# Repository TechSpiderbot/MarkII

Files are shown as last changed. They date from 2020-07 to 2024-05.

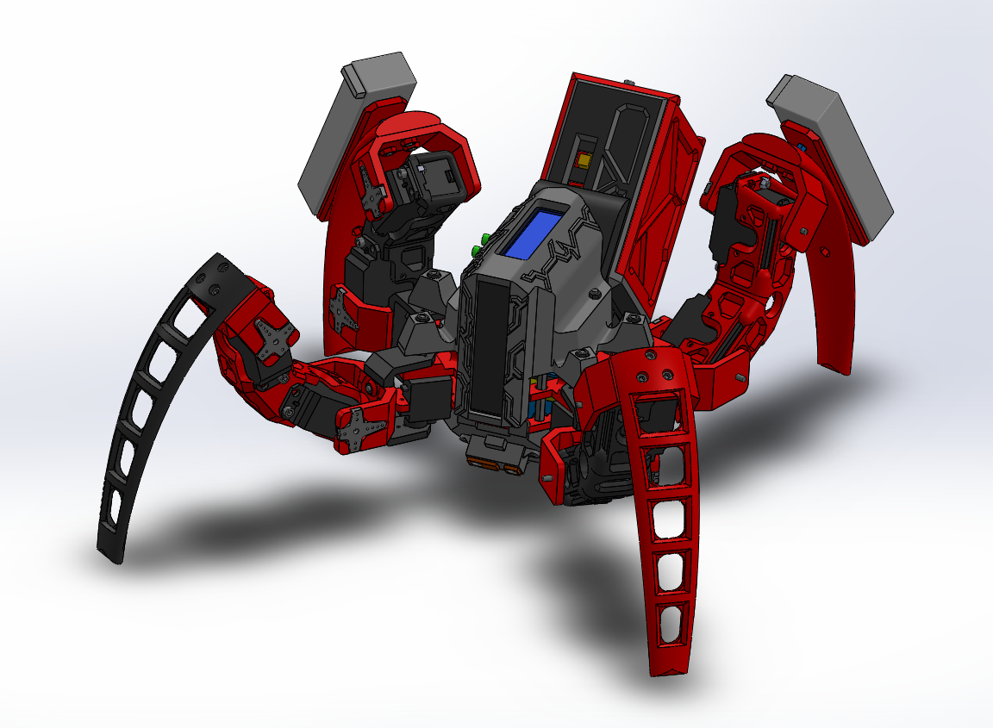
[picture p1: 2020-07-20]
img/mrkII_DES0011.PNG

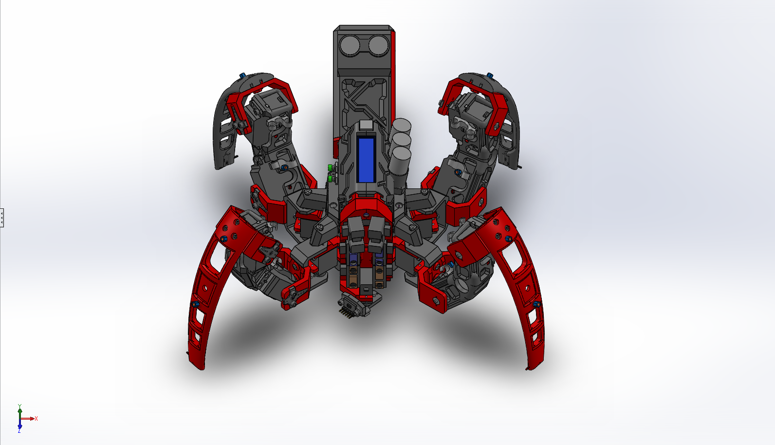
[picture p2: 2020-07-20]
img/mrkII_DES0023.PNG

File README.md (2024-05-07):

# MarkII 

~Scrapped project~

The MrkII TechSpider is an Medium cost, open-source, 3D printed, quadruped robot platform.
The front is designed to be customizable for any type of module. There for the modules can be easily swaped. The cost for the whole robot is around €300. On the backside is a container housing the microcontroller.

The robot is designed for a minimum 3D print build area of 140x140mm
Used material is PLA with a 0.4 nozzle and 30% infill.



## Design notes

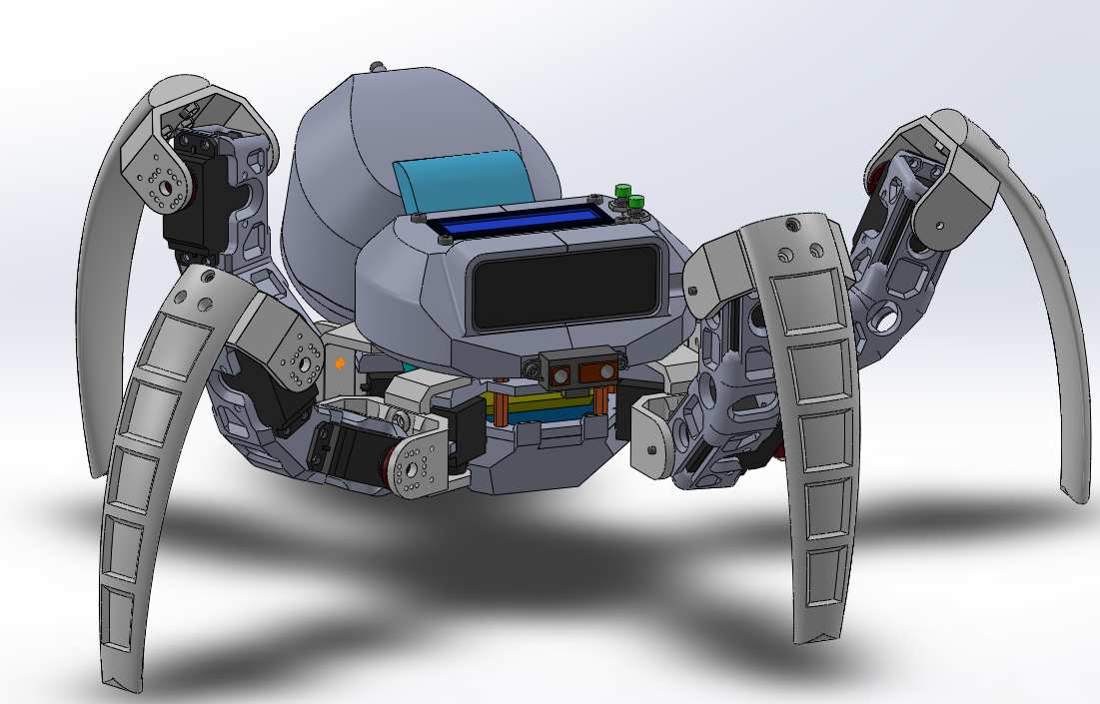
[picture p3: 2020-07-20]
img/mrkII_DES0003.PNG

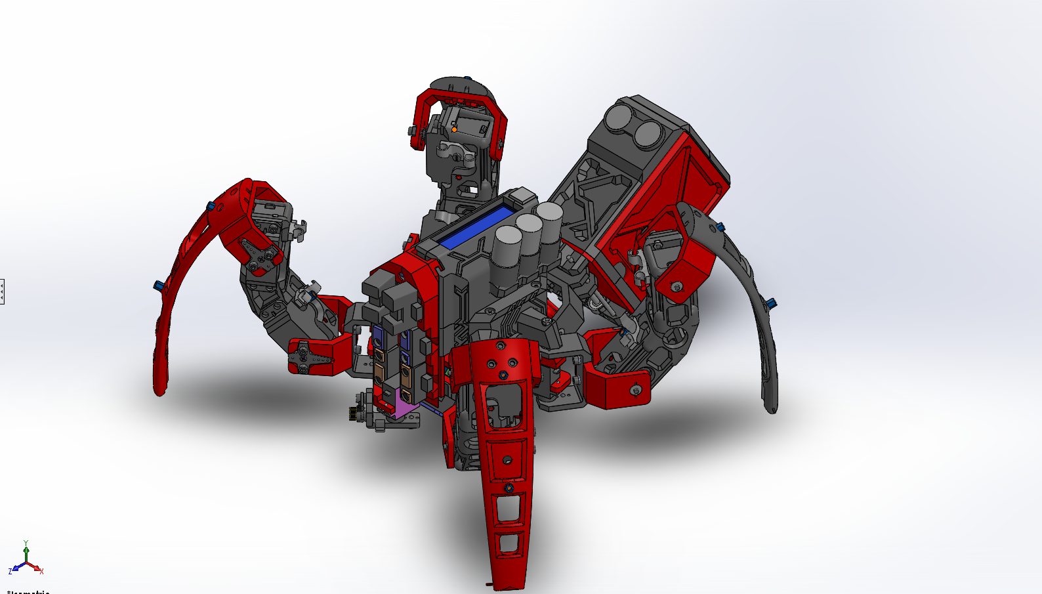
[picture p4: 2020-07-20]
img/mrkII_DES0021.PNG

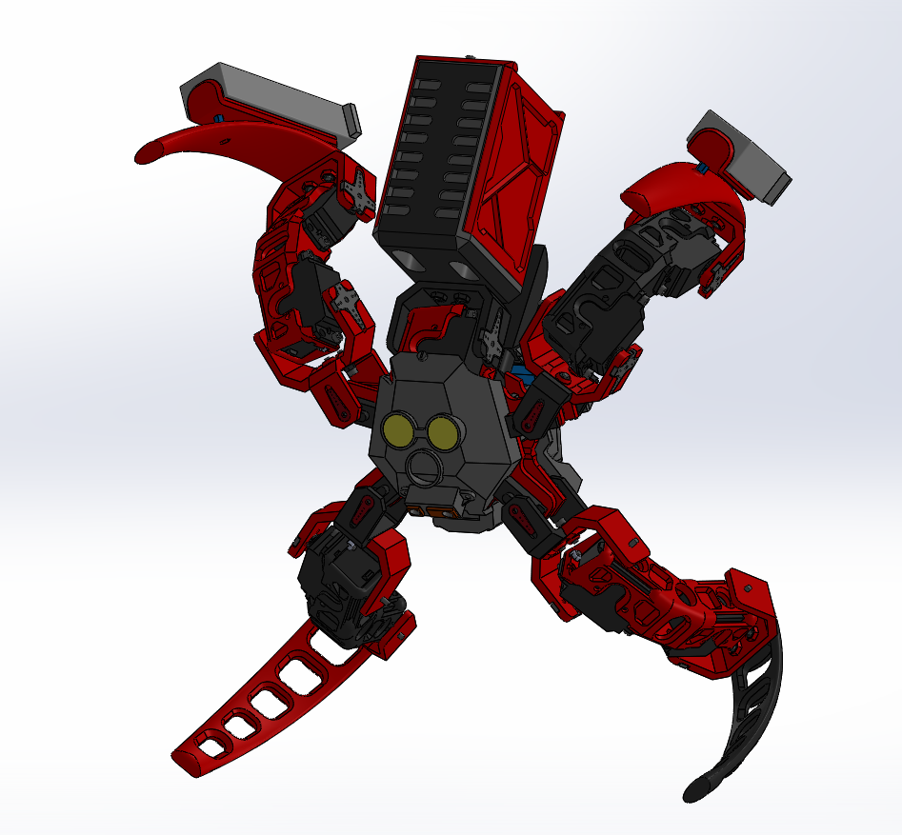
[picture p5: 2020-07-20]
img/mrkII_DES0014.PNG

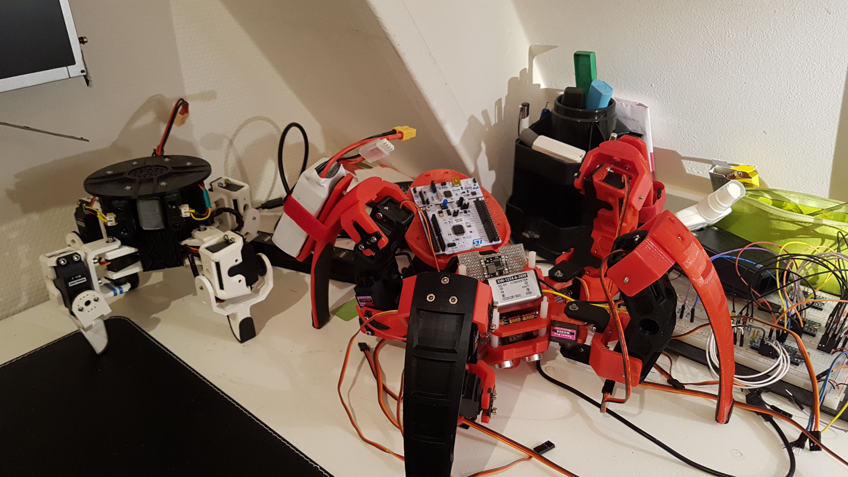
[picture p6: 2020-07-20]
img/mrkII_IMG0003.jpg

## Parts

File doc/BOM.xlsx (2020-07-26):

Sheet: Cover
BOM
Project: | MarkII robot Spider
Versie: | 2.1
Made By: | Geert Huisman
Datum: | 2020-03-12
Printer: | FlashForge Finder
Nozle: | 0.4mm
Type: | PLA
Note: | The front of the robot is customizable! It haves a I2C connection and 3.3V /5V/6V/GND connections for communication and other modules.

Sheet: Hardware
Main Body: |  |  | Type: | count:
 | M2 | round phillips Tapping screw | 5mm | 4
 | M3 | hex inbus | 12mm | 14
 |  | hex inbus | 10mm | 4
 |  | hex inbus | 8mm | 1
 |  | bolt cheese head | 7mm | 4
 |  | round phillips screw | 5mm | 4
 |  | hex flat nut |  | 16
 |  | Nylon Hex Spacers Male to Female | 15+6mm | 18
 |  | Embedded Nuts |  | 11
Parts for single leg
Legs: |  |  | Type: | count:
 | M3 | hex flat nut |  | 9
 |  | hex inbus | 12mm | 5
 |  | hex inbus | 10mm | 2
 |  | hex inbus | 8mm | 2
 |  | round phillips screw | 5mm | 2
 |  | Spring washers |  | 2
 |  | HTSB (spacers) | 5mm | 3
 |  | F693ZZ (bearing) | 3x8x4mm | 3
 |  | Hex Self Tapping scews | 6mm | 5
 |  | bolt | 8mm | 1
 |  | Embedded Nuts |  | 8
 |  | old bike inner tire (used for grip pads on the legs)
Back Body: |  |  | Type: | count:
 | M4 | hex flat nut
 | M3 | hex inbus | 12mm | 12
 |  | hex flat nut |  | 6
 |  | Embedded Nuts |  | 4
 |  | 624ZZ (bearing) | 4x13x5mm | 1
 |  | Nylon Hex Spacers Male to Female | 15+6mm | 2
 |  | socket Hexagon Hex Self Head Tapping scews | 6mm | 2
 |  | F693ZZ (bearing) | 3x8x4mm | 1
 | 3mm | rod from a pc dvd-drive | 82.5mm | 2
 | M1 | bolt | 6mm | 2
 |  | N35 Round Magnet | 10x2 | 1
Front Body: |  |  | Type: | count:
 | M3 | Embedded Nuts |  | 3
 |  | hex inbus | 8mm | 5

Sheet: TOTAL_HARDWARE
 | Type: | Size: | count:
M1 | bolt | 6mm | 2
M2 | round phillips Tapping screw | 5mm | 4
M3 | hex inbus | 12mm | 46
 | hex inbus | 10mm | 12
 | hex inbus | 8mm | 12
 | hex inbus | 6mm | 2
 | Spring washers |  | 8
 | hex flat nut |  | 60
 | Embedded Nuts |  | 50
 | bolt cheese head | 7mm | 8
 | round phillips screw | 5mm | 8
 | socket Hexagon Hex Self Head Tapping scews | 6mm | 22
 | Nylon Hex Spacers Male to Female | 15+6mm | 20
 | HTSB (spacers) | 5mm | 12
M4 | 624ZZ (bearing) | 4x13x5mm | 13
 | hex flat nut |  | 1
Other
3mm | rod from a pc dvd-drive | 82.5mm | 2
 | N35 Round Magnet | 10x2 | 1
 | old bike inner tire (used for grip pads on the legs) |  | 1

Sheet: 3D Printed Parts
Main Body: |  | Count:
 | BODY_arduinoNanoBracket | 1x
 | BODY_capBot | 1x
 | BODY_capTop | 1x
 | BODY_displayClips | 2x
 | BODY_frame1 | 1x
 | BODY_frame2 | 1x
 | BODY_frame3 | 1x
 | BODY_PS2Bracket | 1x
 | BODY_servoBracket1 (embedded nuts) | 1x | (There are 2 versions that can be used "bracket1" or "bracket2" the differents are: one uses embedded nuts while the other uses flat nuts)
 | BODY_servoBracket2
Legs:
 | TIBIA | 4x
 | TIBIA_bracket | 4x
 | TIBIA_batteryHolder | 4x
 | FEMUR | 4x
 | FEMUR_bracket | 4x
 | COXA_bracket | 4x
 | Single_cable_bracket | 8x | (There are 2 versions that can be used "Single" or "Duo" cable brackets)
 | Duo_cable_bracket
Back Body:
 | CONTAINER | 1x
 | CONTAINER_sidePlate | 1x
 | CONTAINER_plate | 1x
 | CONTAINER_railBotBracket | 1x
 | CONTAINER_railTopBracket | 1x
 | CONTAINER_railGlider | 1x
 | CONTAINER_bracket | 1x
Front Body:
 | HEAD_slide | 1x
 | HEAD_module1 | 1x
 | HEAD_moduleArm | 1x

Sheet: Electronic components
Main Body: |  | Count: | Example price
 | HC-SR04 Ultrasone sensor | 1 | €2.50 | €2.50
 | MG996R 55g Gear Servo Motor | 1 | €3.60 | €3.60
 | MPU-6050 | 1 | €1.17 | €1.17
 | GP2Y0A41SK0F | 1 | €5.00 | €5.00
 | PCA9685 16 Channel 12bit PWM Servo motor Driver (https://www.ebay.com/itm/PCA9685-16-Channel-12bit-PWM-Servo-motor-Driver-I2C-Module-Robot-ASS/263464876539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) | 1 | €2.28 | €2.28
 | DC12V To DC6V 6A 36W Aluminum Step Down Power Supply (https://www.ebay.com/itm/DC12V-To-DC6V-6A-36W-Aluminum-Step-Down-Power-Supply-Converter-Regulator-Module/182827563833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) | 1 | €5.00 | €5.00
 | Arduino Nano | 2 | €3.50 | €7.00
 | PS2 Controller kit | 1 | €10.00 | €10.00
 | Custom cable distribution pcb | 1 | €5.00 | €5.00
 | Custom signal pcb | 1 | €5.00 | €5.00
 | Lockless Momentary ON/OFF Push button Switch | 2 | €2.25 | €4.50
 | I2C Interface 16X2 Character LCD Module Display (blue) | 1 | €3.00 | €3.00
 | GY-271 HMC5883L triple Compas | 1 | €4.00 | €4.00
 | WT61 (advanced compass) | 1 | €31.00 | €31.00
 | 25V 10000uF High Frequency Elcos 18x35mm | 3 | €1.70 | €5.10
Parts for single leg
Legs: | Type: | Count:
 | MG996R 55g Gear Servo Motor | 1 | €3.60 | €3.60
 | ~~VS-2 servo motor (hobby servo)~~ | ~~1~~ | €0.00 | €0.00
 | MG90S Micro Metal Gear 9g Servo (screws for mounting is included) | 1 | €3.50 | €3.50
 | 1.27mm Pitch 16 Pin Flat IDC Ribbon (flatcable for extention)
 | Cable sleeve M3
 | High Accuracy 10g-1kg Pressure Sensor Smart Flexible Thin Film Force Sensor | 1 | €4.50 | €4.50
 | Custom sensor pcb | 1 | €5.00 | €5.00
Back Body:
 | M4 GA12 N20 DC (500RPM) 100mm/6V | 1 | €5.00 | €5.00
 | NUCLEO-F411RET6 | 1 | €20.00 | €20.00
 | DRV8833 motor driver | 1 | €1.70 | €1.70
 | Mini Push Button Switch | 1 | €1.19 | €1.19
 | HC-SR04 Ultrasone sensor | 1 | €2.55 | €2.55
 | NRF24L01 2.4Ghz | 2 | €3.80 | €7.60
Front Body: |  | Count:
 | Arduino Nano | 1 | €3.50 | €3.50
 | GP2Y0A41SK0F | 2 | €5.00 | €10.00
 | GP2Y0A21YK0F | 2 | €5.00 | €10.00
 | GP2Y0A02YK0F | 2 | €6.50 | €13.00
 | GY-VL53L0XV2 Time of flight distance sensor (https://www.ebay.com/itm/GY-VL53L0XV2-VL53L0X-Time-of-Flight-Distance-Sensor-Breakout-Module/322328103831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) | 1 | €7.00 | €7.00
 | MG90S Micro Metal Gear 9g Servo (screws for mounting is included) | 1 | €3.60 | €3.60
 | Custom signal pcb | 1 | €5.00 | €5.00
 |  |  | €171.44 | €200.89 | Totall

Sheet: TOTAL_ELECTRONICS
Module: | Count:
raspberry pi + sd card | 1
arduino pro mini | 2
NRF24L01 | 2
Arduino Nano | 3
MG996R 55g Gear Servo Motor | 5
MG90S Micro Metal Gear 9g Servo (screws for mounting is included) | 5
VS-2 servo motor (hobby servo) | 4 | (If unable to find these sevos, it's also possible to use the MG996R instead )
HC-SR04 Ultrasone sensor | 2
MPU-6050 | 1
PS2 Controller kit | 1
Lockless Momentary ON/OFF Push button Switch | 2
I2C Interface 16X2 Character LCD Module Display (blue) | 1
GY-271 HMC5883L triple Compas | 1
25V 10000uF High Frequency Elcos 18x35mm | 3
High Accuracy 10g-1kg Pressure Sensor Smart Flexible Thin Film Force Sensor | 4
PCA9685 16 Channel 12bit PWM Servo motor Driver (https://www.ebay.com/itm/PCA9685-16-Channel-12bit-PWM-Servo-motor-Driver-I2C-Module-Robot-ASS/263464876539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) | 1
DC12V To DC6V 6A 36W Aluminum Step Down Power Supply (https://www.ebay.com/itm/DC12V-To-DC6V-6A-36W-Aluminum-Step-Down-Power-Supply-Converter-Regulator-Module/182827563833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) | 1
M4 GA12 N20 DC (500RPM) 100mm/6V | 1
DRV8833 motor driver | 1
Mini Push Button Switch | 1
GY-VL53L0XV2 Time of flight distance sensor (https://www.ebay.com/itm/GY-VL53L0XV2-VL53L0X-Time-of-Flight-Distance-Sensor-Breakout-Module/322328103831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) | 1
GP2Y0A41SK0F | 3
GP2Y0A21YK0F | 2
GP2Y0A02YK0F | 2
NRF24L01 2.4Ghz | 2 | (wire less comunication for future updates)
NUCLEO-F411RET6 | 1
Custom signal front pcb | 2
Custom sensor pcb | 4
Custom cable distribution pcb | 1
1.27mm Pitch 16 Pin Flat IDC Ribbon (flatcable for extention)
Cable sleeve M3

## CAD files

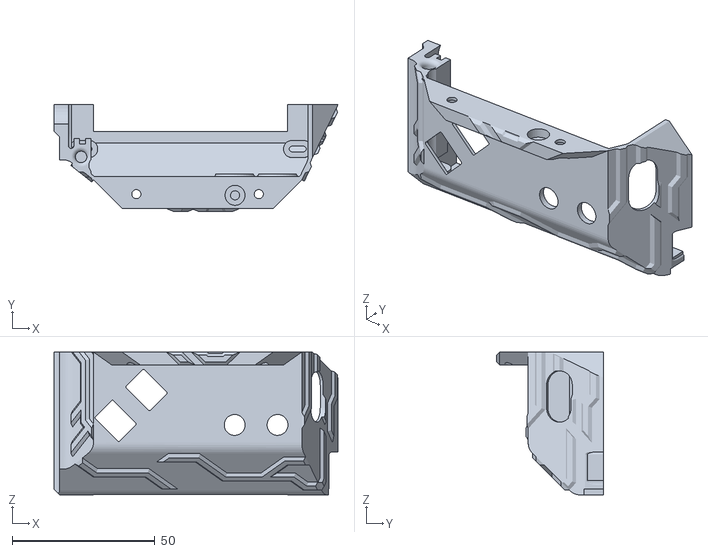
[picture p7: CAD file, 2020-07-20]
cad/0_Main bodyDesign/BODY_capTop/BODY_rightTop.STL
99.4 x 37.3 x 50.0

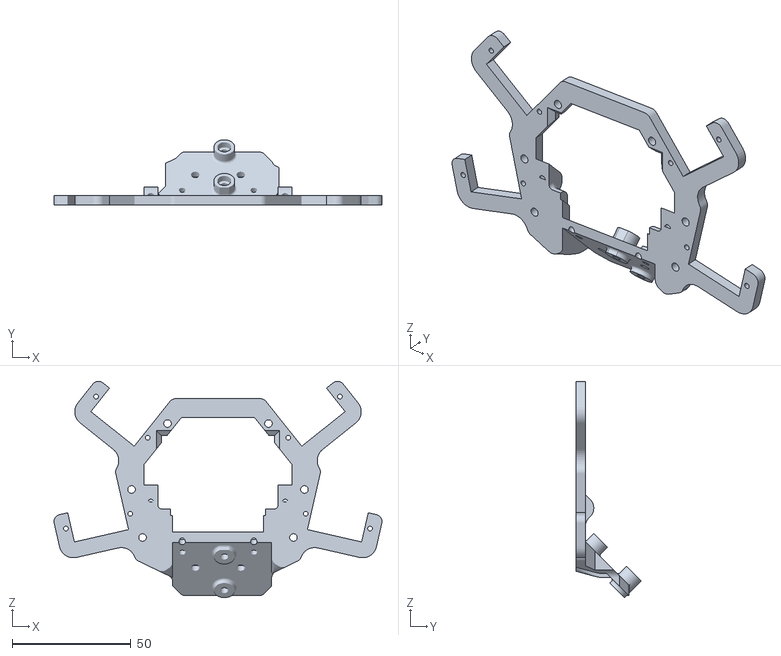
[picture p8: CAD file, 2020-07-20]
cad/0_Main bodyDesign/BODY_frame1.STL
137.9 x 27.5 x 90.9

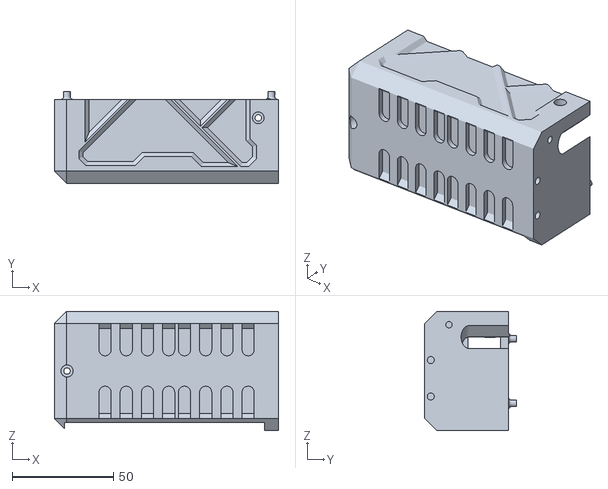
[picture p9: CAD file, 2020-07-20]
cad/1_Back bodyDesign/CONTAINER/CONTAINER_bot.STL
110.8 x 45.3 x 59.0

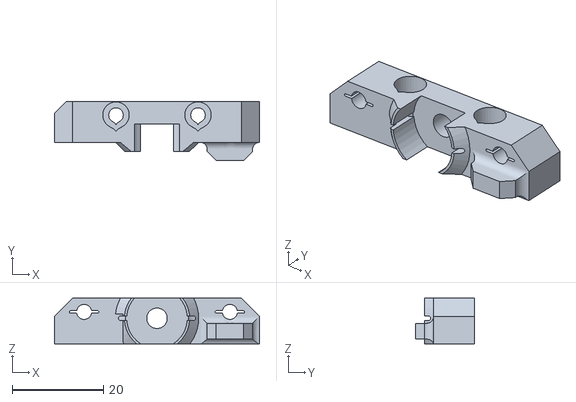
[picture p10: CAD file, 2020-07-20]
cad/1_Back bodyDesign/CONTAINER_railBotBracket.STL
45.0 x 13.0 x 10.00

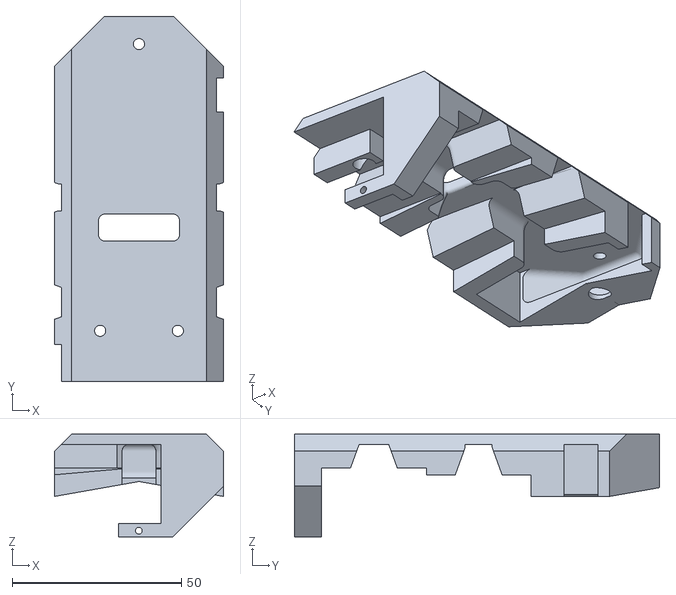
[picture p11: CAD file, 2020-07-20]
cad/2_Front bodyDesign/HEAD_module1.STL
50.0 x 108.0 x 30.4

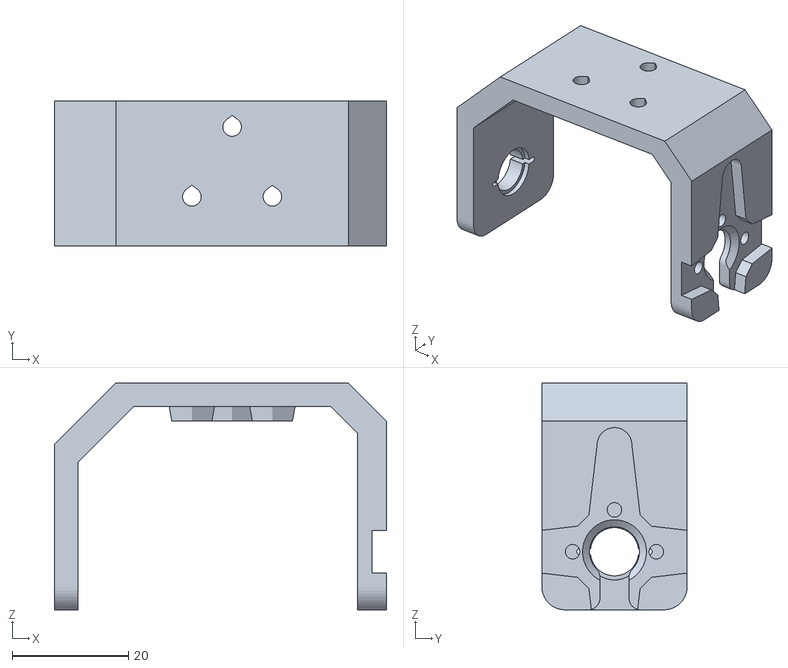
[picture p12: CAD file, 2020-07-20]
cad/3_legDesign/TIBIA_bracket.STL
57.1 x 25.0 x 39.0

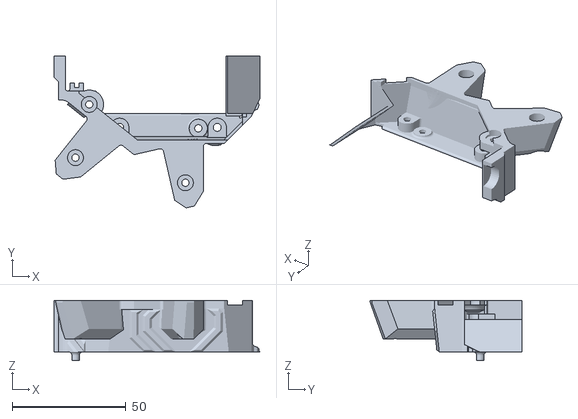
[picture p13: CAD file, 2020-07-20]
cad/0_Main bodyDesign/BODY_capTop/BODY_rightBot.STL
90.5 x 66.7 x 26.4

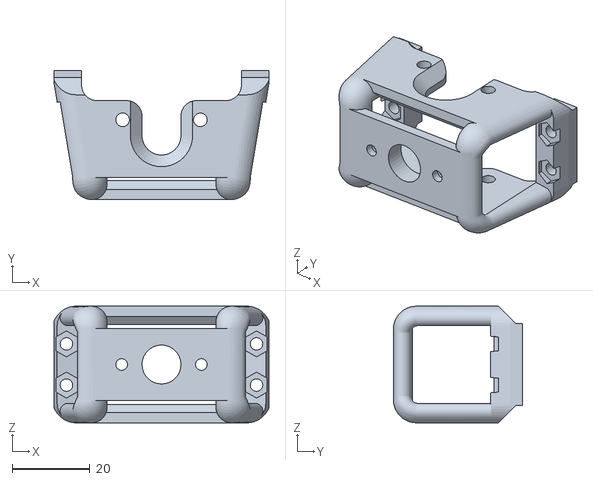
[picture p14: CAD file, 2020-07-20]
cad/0_Main bodyDesign/BODY_servoBracket1.STL
55.3 x 33.3 x 30.0

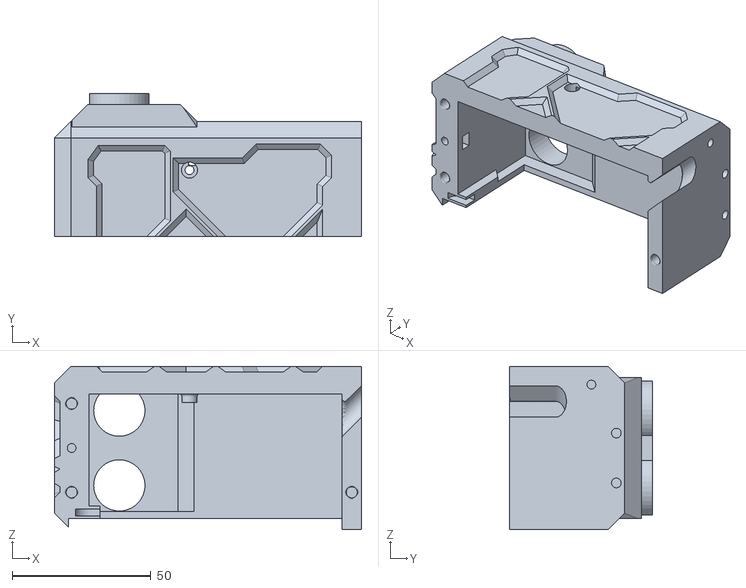
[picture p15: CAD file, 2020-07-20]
cad/1_Back bodyDesign/CONTAINER/CONTAINER_top.STL
110.8 x 51.5 x 59.0

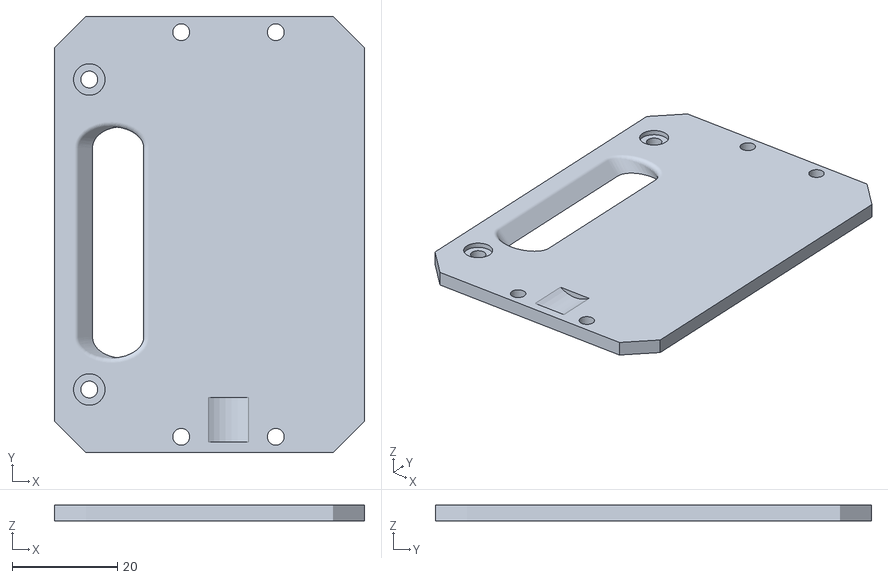
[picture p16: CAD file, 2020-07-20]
cad/1_Back bodyDesign/CONTAINER_plate.STL
59.0 x 83.0 x 3.00

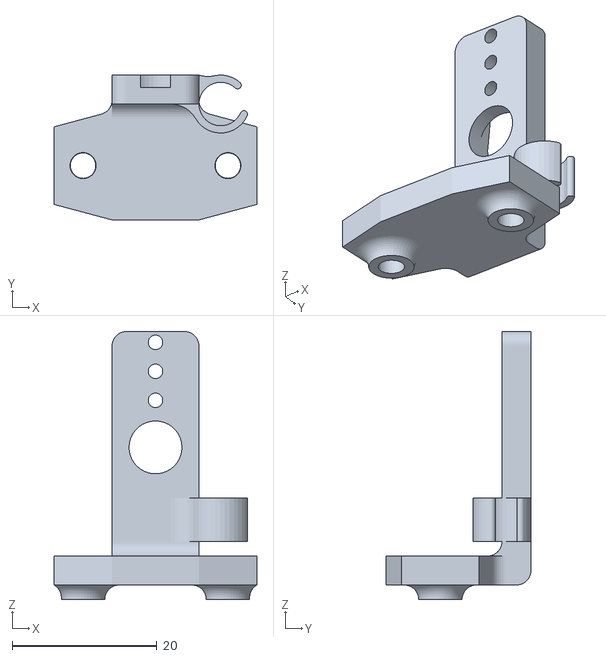
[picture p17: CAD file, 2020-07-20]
cad/2_Front bodyDesign/HEAD_moduleArm.STL
28.0 x 20.0 x 37.0

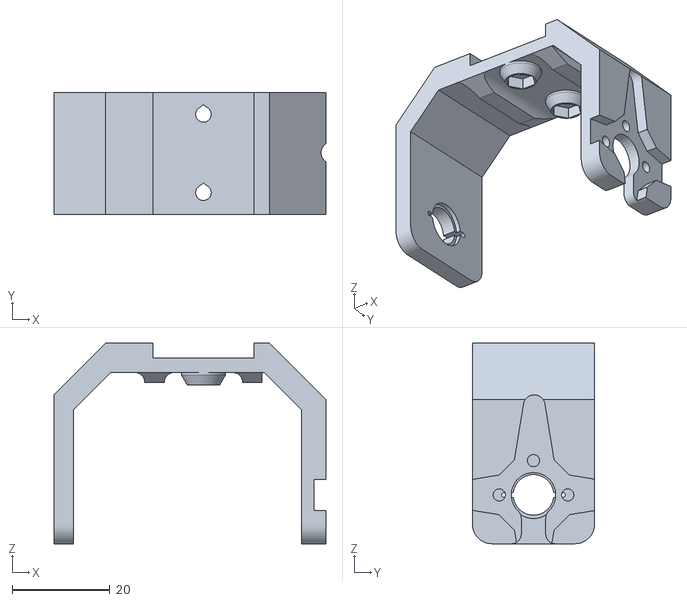
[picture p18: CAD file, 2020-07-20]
cad/3_legDesign/FEMUR_bracket.STL
55.6 x 25.0 x 41.0

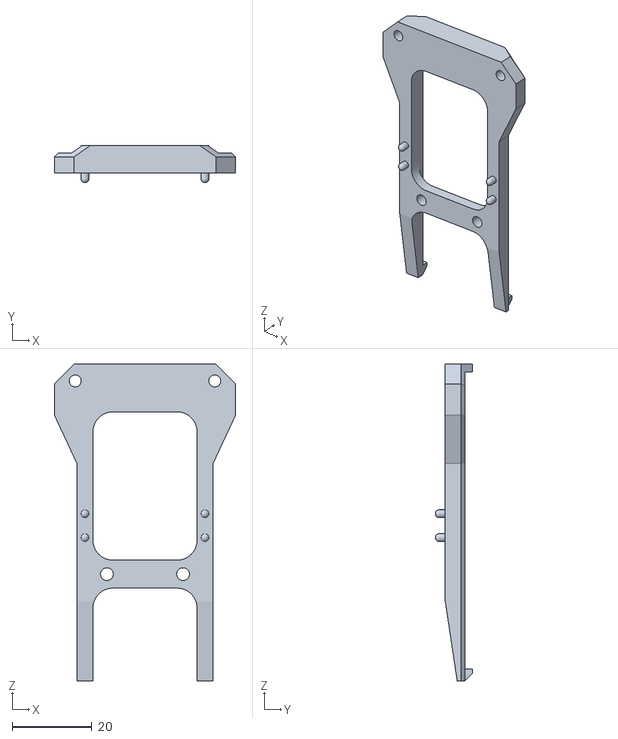
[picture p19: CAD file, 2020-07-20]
cad/0_Main bodyDesign/BODY_PS2Bracket.STL
45.5 x 9.40 x 79.5

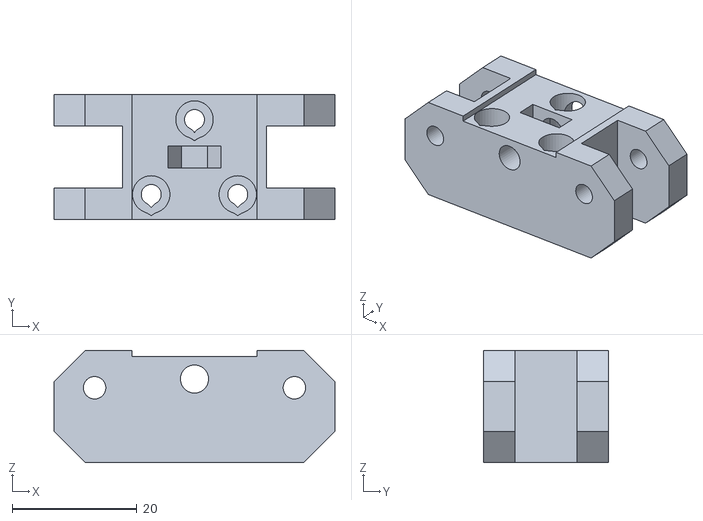
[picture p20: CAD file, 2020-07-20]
cad/1_Back bodyDesign/CONTAINER_railGlider.STL
45.0 x 20.0 x 18.0

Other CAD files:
cad/0_Main bodyDesign/BODY_capTop/BODY_leftBot.STL
cad/2_Front bodyDesign/HEAD_slide.STL
cad/3_legDesign/Single_cable_bracket.STL
cad/0_Main bodyDesign/BODY_capTop/BODY_leftTop.STL
cad/0_Main bodyDesign/BODY_arduinoNanoBracket.STL
cad/0_Main bodyDesign/BODY_capBot.STL
cad/0_Main bodyDesign/BODY_displayClips.STL
cad/0_Main bodyDesign/BODY_frame2.STL
cad/0_Main bodyDesign/BODY_frame3.STL
cad/0_Main bodyDesign/BODY_servoBracket2.STL
cad/1_Back bodyDesign/CONTAINER_bracket.STL
cad/1_Back bodyDesign/CONTAINER_railTopBracket.STL
cad/1_Back bodyDesign/CONTAINER_sidePlate.STL
cad/3_legDesign/COXA_bracket.STL
cad/3_legDesign/Duo_cable_bracket.STL
cad/3_legDesign/FEMUR.STL
cad/3_legDesign/TIBIA.STL
cad/3_legDesign/TIBIA_batteryHolder.STL
cad/5_Shield/shield_cap_2.SLDDRW
cad/5_Shield/shield_plate.SLDDRW

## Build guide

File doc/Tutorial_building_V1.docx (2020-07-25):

Tutorial_Building

Body assembly

Author | Version
Geert Huisman | Setup

Requirements
Hardware M3 | | Amount
| hex flat nut | 9x
12mm | hex inbus | 5x
10mm | hex inbus | 2x
8mm | hex inbus | 2x
5mm | round phillips screw | 4x
| ~~Spring washers~~ | ~~2x~~
5mm | HTSB (spacers) | 3x
3x8x4mm | F693ZZ (bearing) | 2x
6mm | Hex Self Tapping screws | 5x
8mm | bolt | 1x
| Embedded Nuts | 8x
| old bike inner tire (Rubber is used for grip pads on the legs with some glue) | 1x
3D parts | | Amount
| TIBIA | 4x
| TIBIA_bracket | 4x
| TIBIA_batteryHolder | 2x
| FEMUR | 4x
| FEMUR_bracket | 4x
| COXA_bracket | 4x
| Single_cable_bracket (Optional ) | 8x
| Duo_cable_bracket
Electronics | | Amount
| MG996R 55g Gear Servo Motor | 2x
50cm | 1.27mm Pitch 16 Pin Flat IDC Ribbon (flatcable for extention) | 3x
50cm | Cable sleeve M3 | 1x
| High Accuracy 10g-1kg Pressure Sensor Smart Flexible Thin Film Force Sensor | 1x
| Custom pcb (Leg Distr sensor) | 1x
100cm | L125BL25 0.25mm² wire | 6x
15cm | L125BL25 0.25mm² wire | 2x

1. LEGS 4x

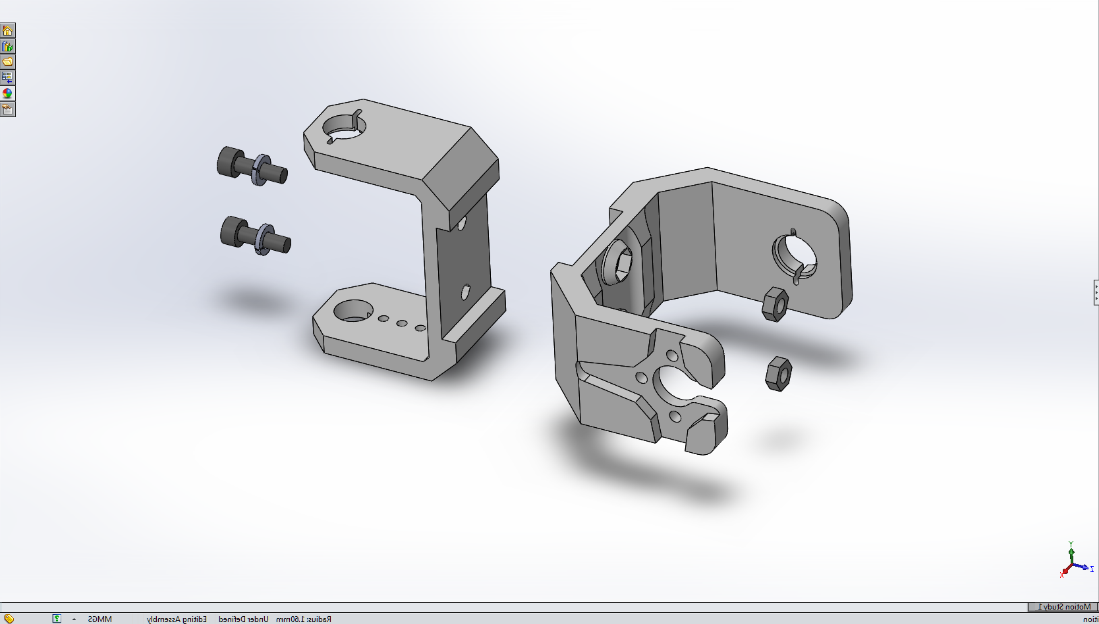
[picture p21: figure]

| 8mm hex inbus hex flat nut ~~Spring washers~~ | 2x 2x ~~2x~~

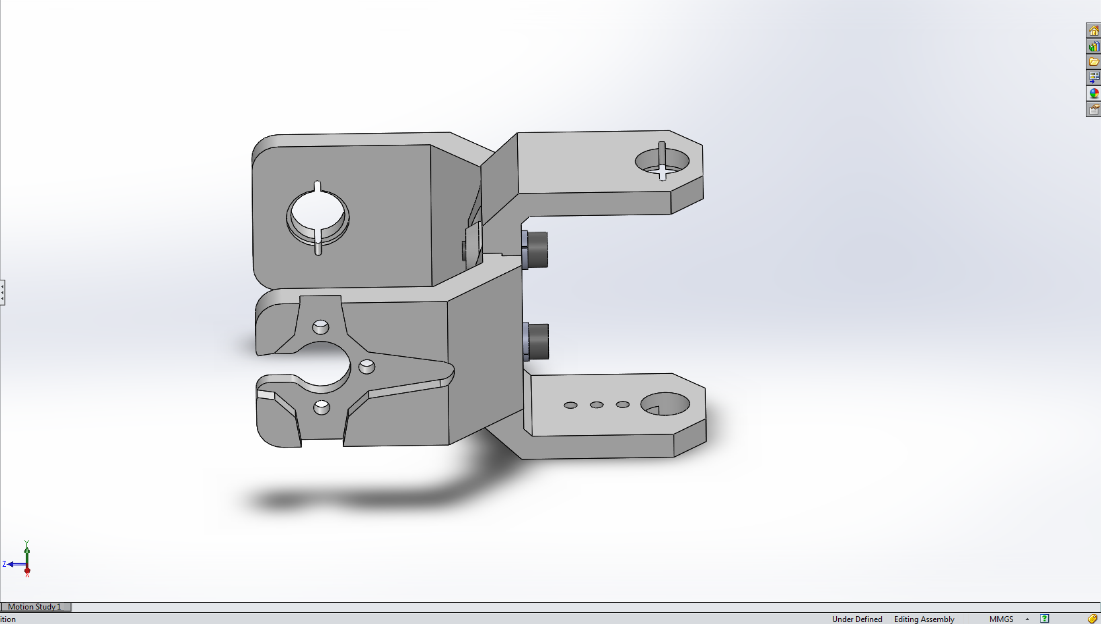
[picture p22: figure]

| Assembly view

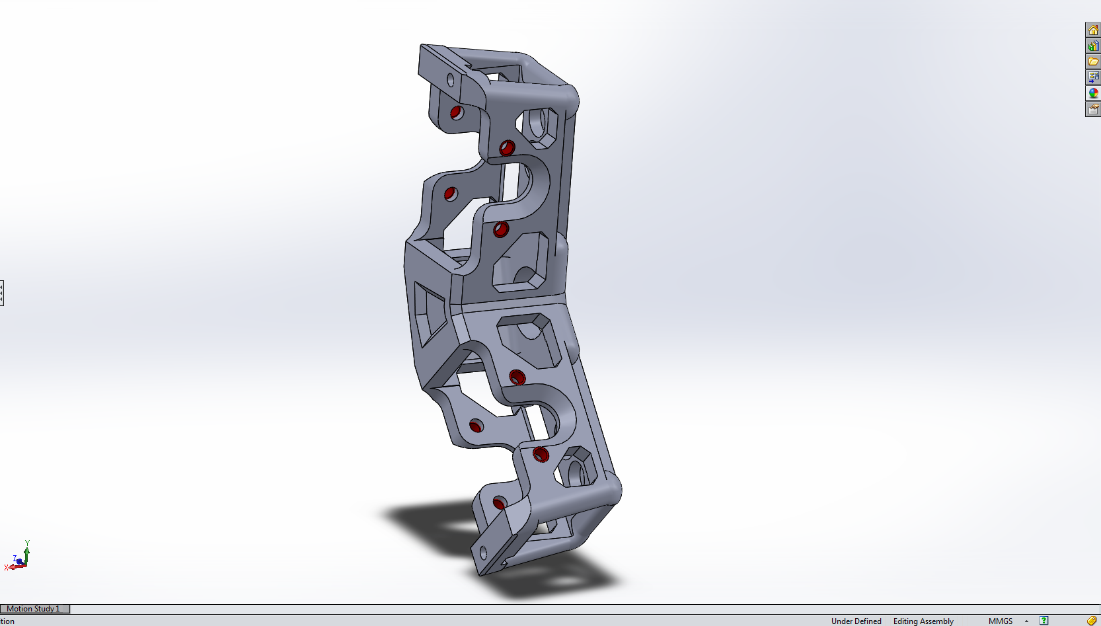
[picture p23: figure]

| Embedded Nuts | 8x

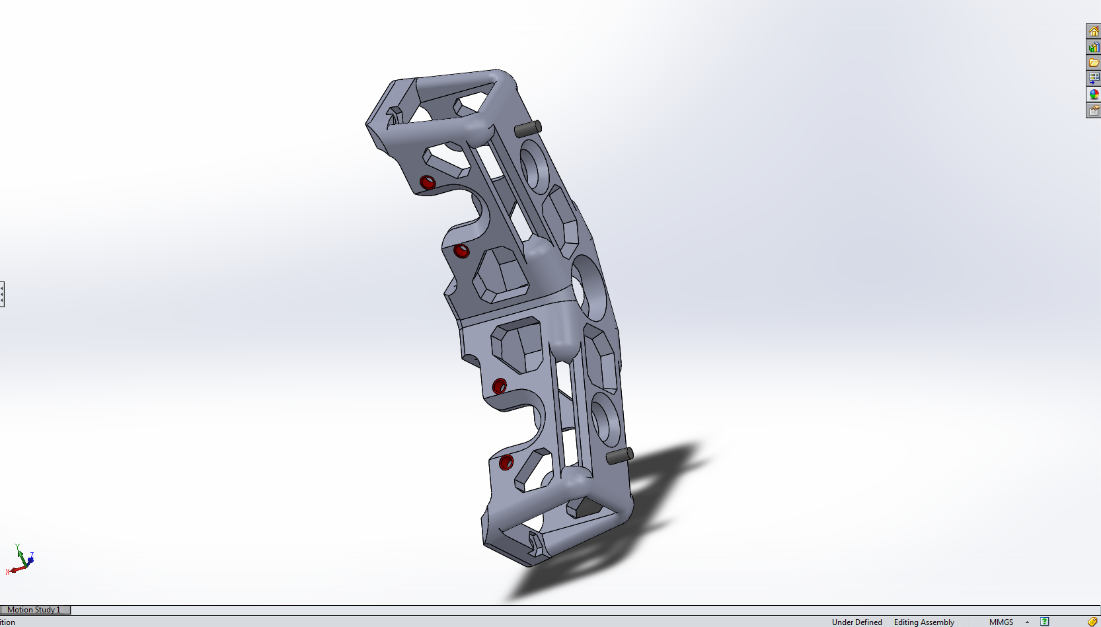
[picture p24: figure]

| 10mm hex inbus | 2x

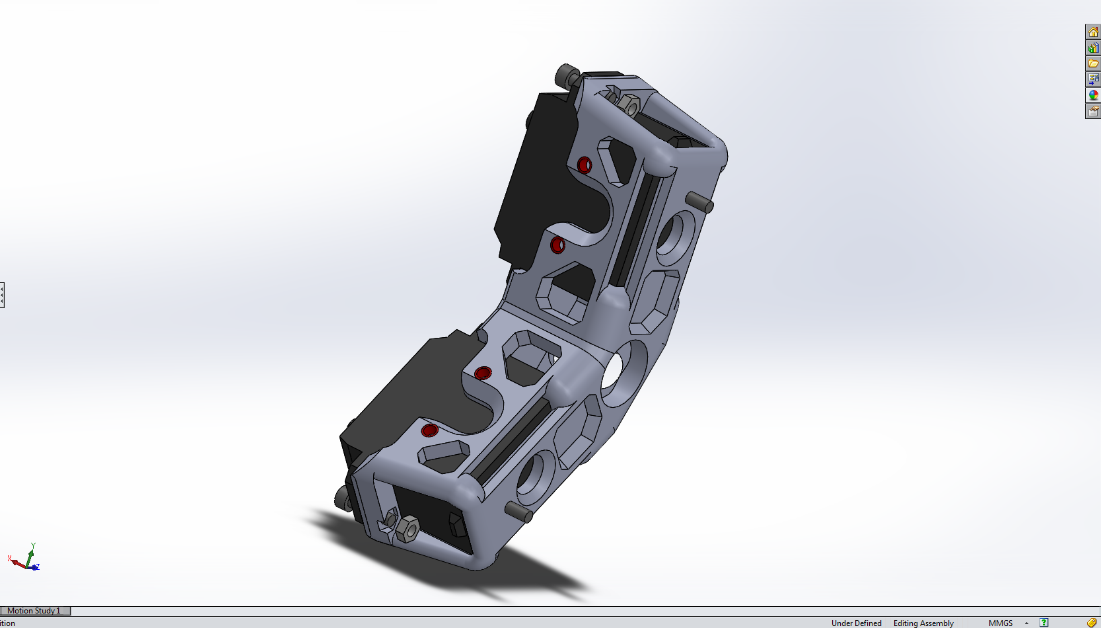
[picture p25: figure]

| MG996R 55g Gear Servo Motor hex flat nut 12mm hex inbus | 2x 2x 2x

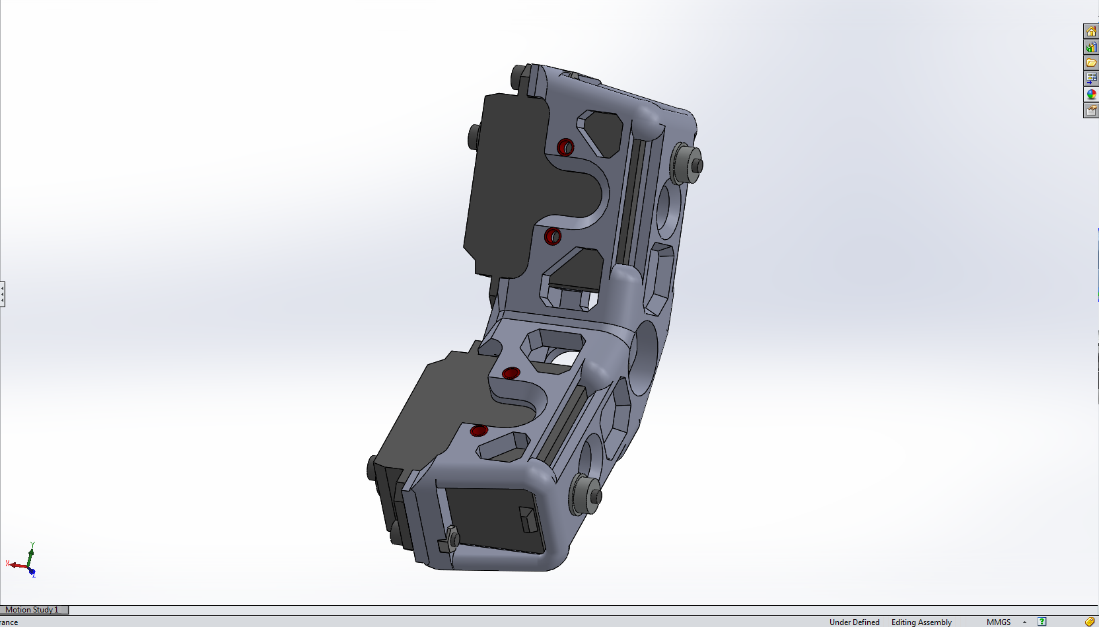
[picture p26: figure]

| 3x8x4mm F693ZZ (bearing) | 2x

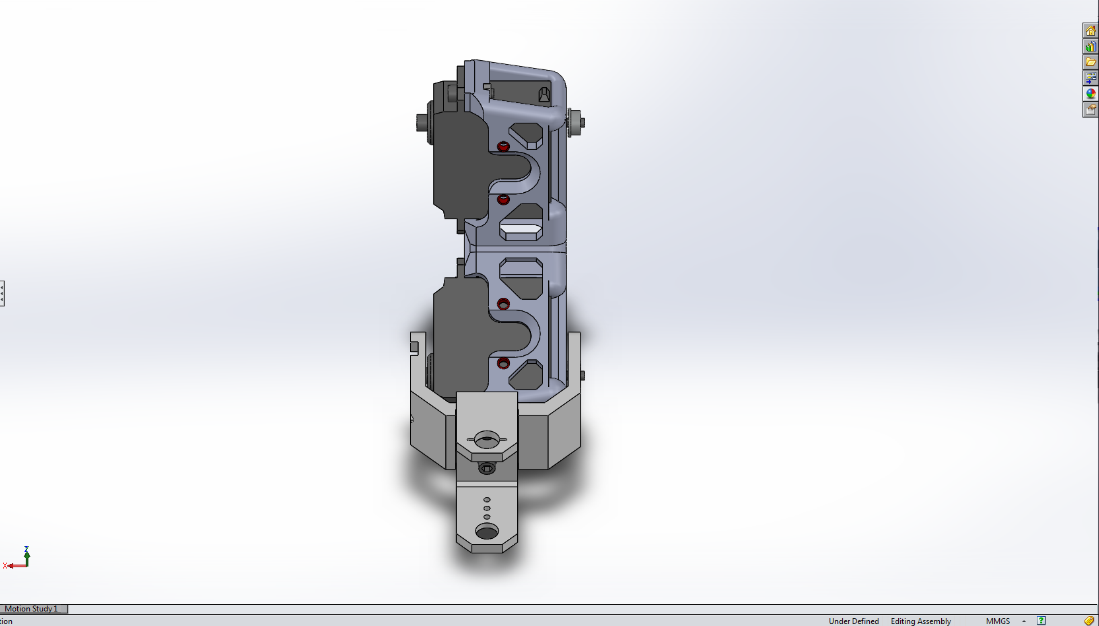
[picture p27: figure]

| Assembly view

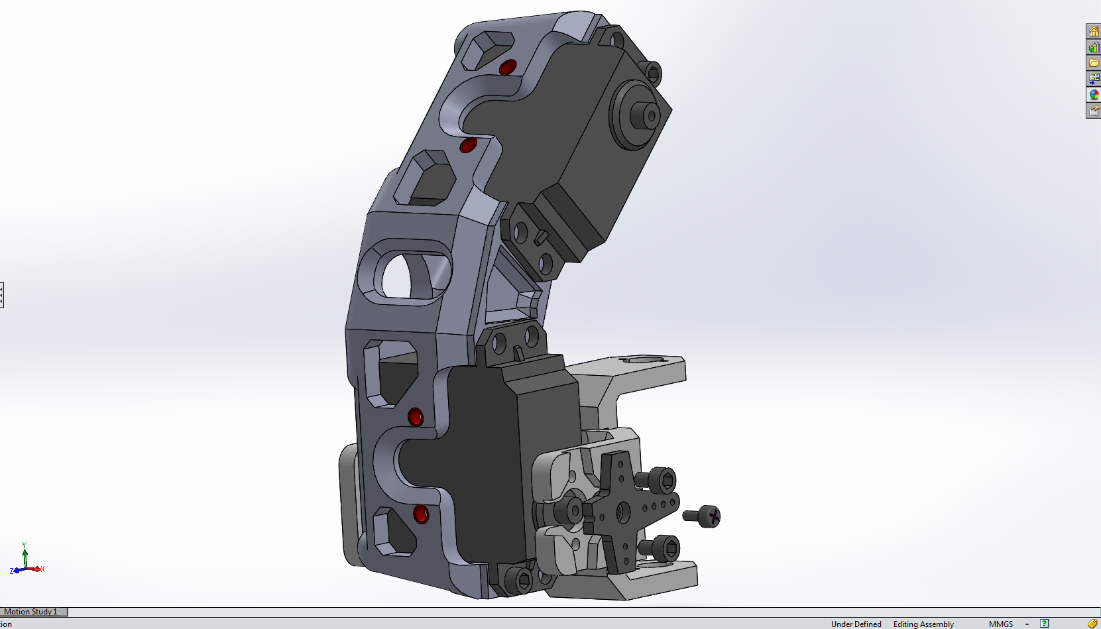
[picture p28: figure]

| (90o in the up position, see picture. Make sure the servo axle is turned 180o) Servo horn 6mm Hex Self Tapping screws | 1x 2x

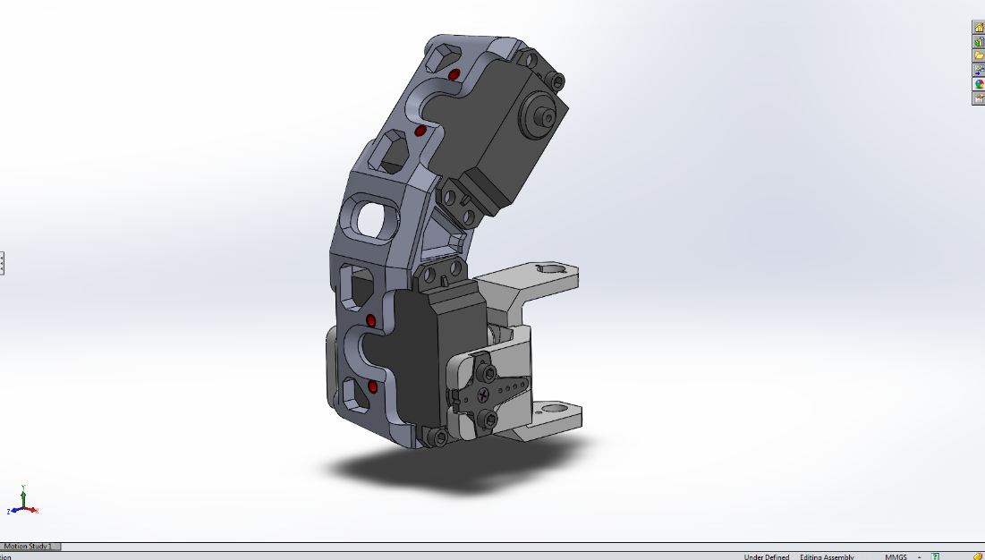
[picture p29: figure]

| Assembly view

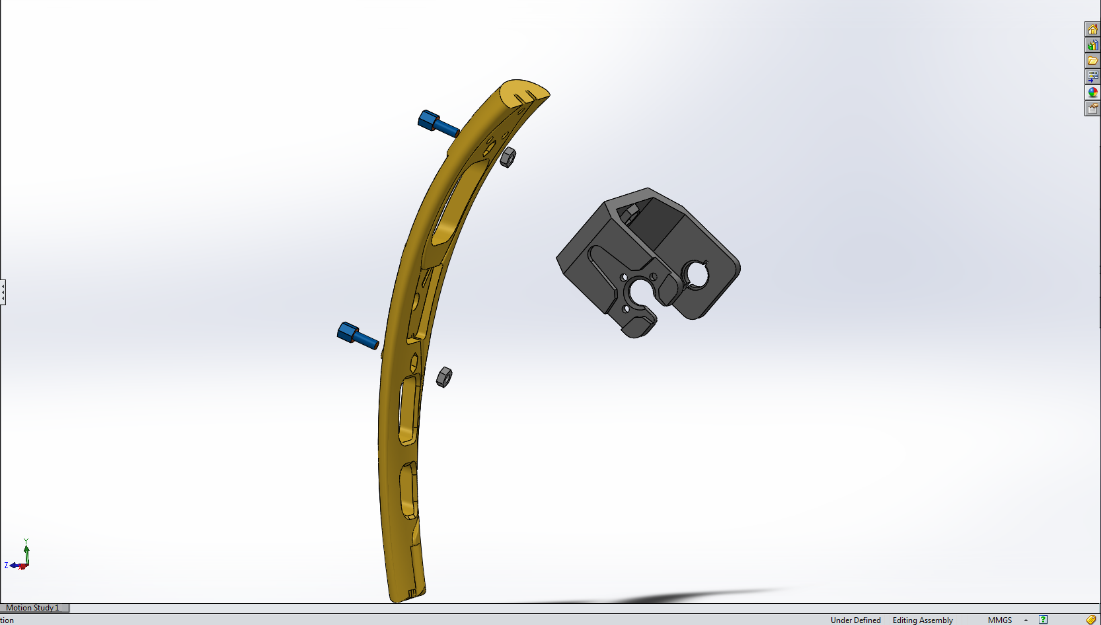
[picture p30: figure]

| hex flat nut 5mm HTSB (spacers) | 2x 2x

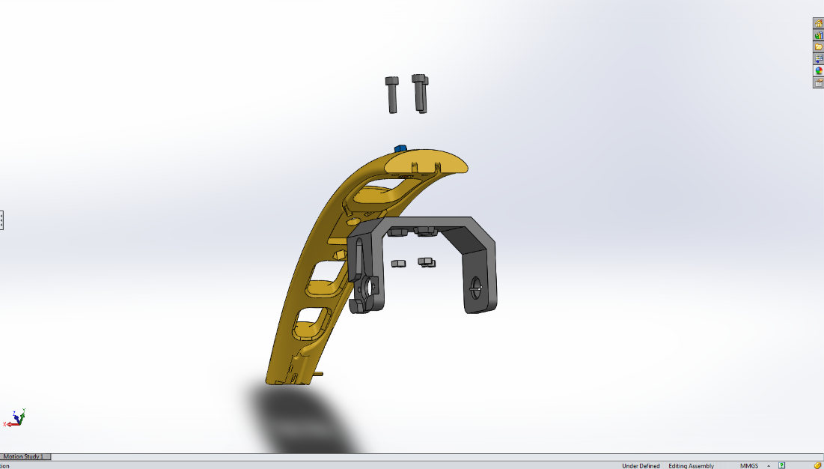
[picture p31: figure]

| hex flat nut 12mm hex inbus | 3x 3x

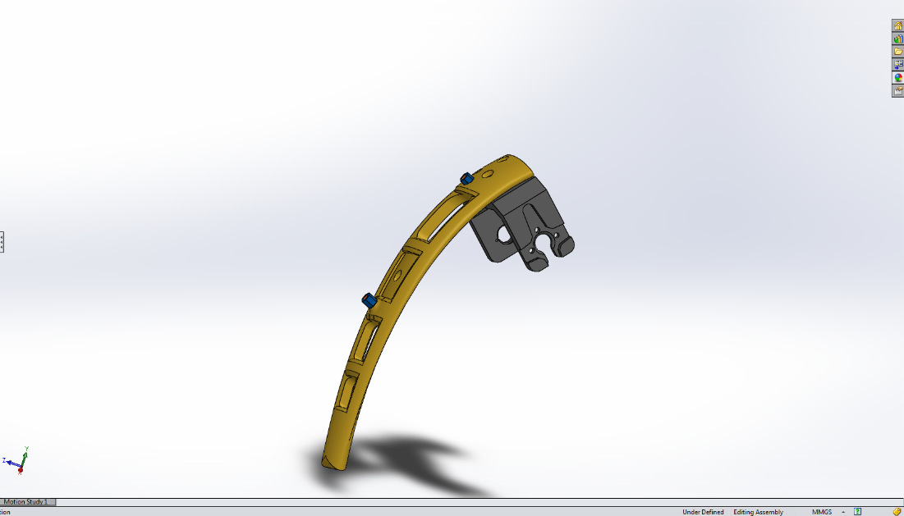
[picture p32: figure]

| Assembly view

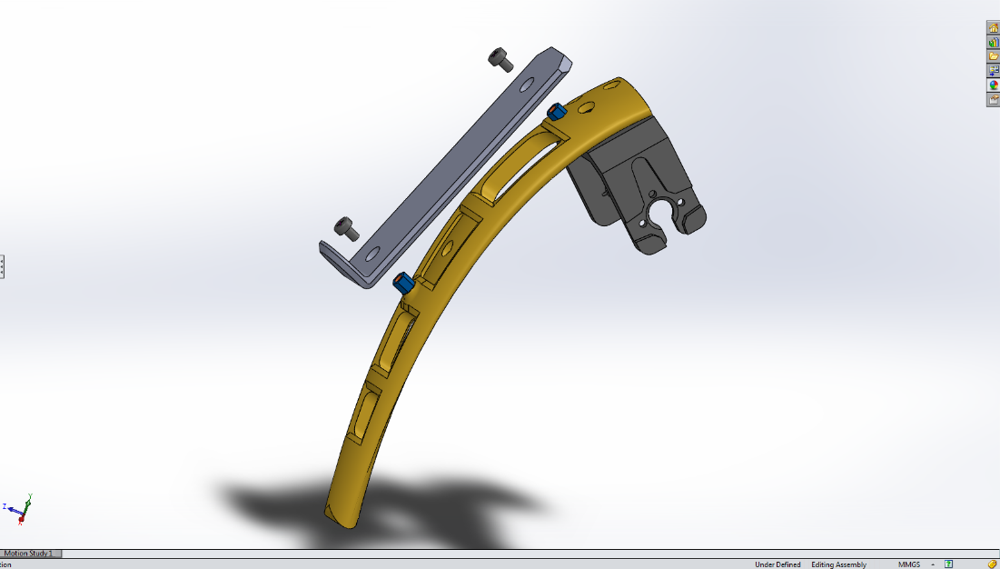
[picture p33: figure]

| round phillips screw | 2x

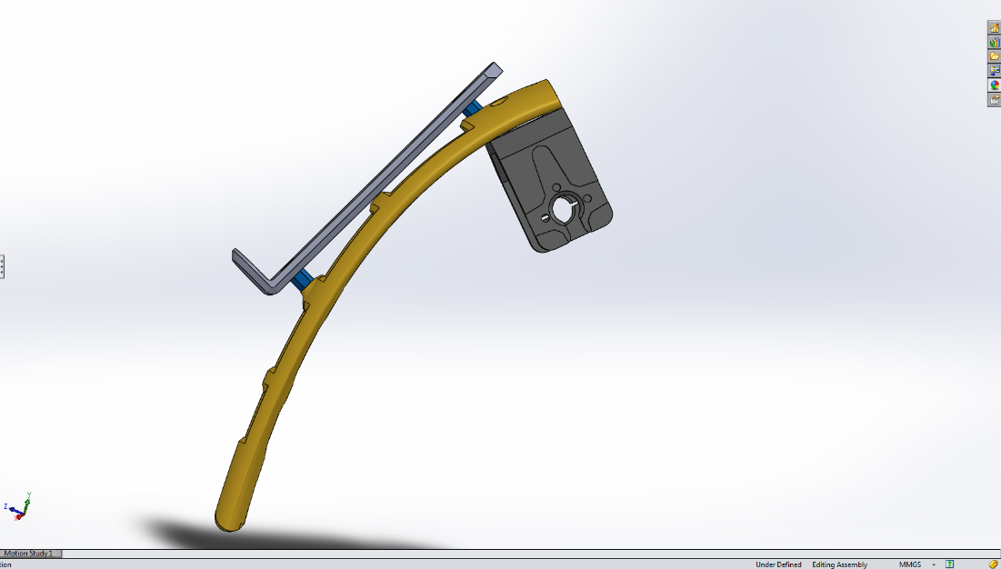
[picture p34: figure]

| Assembly view

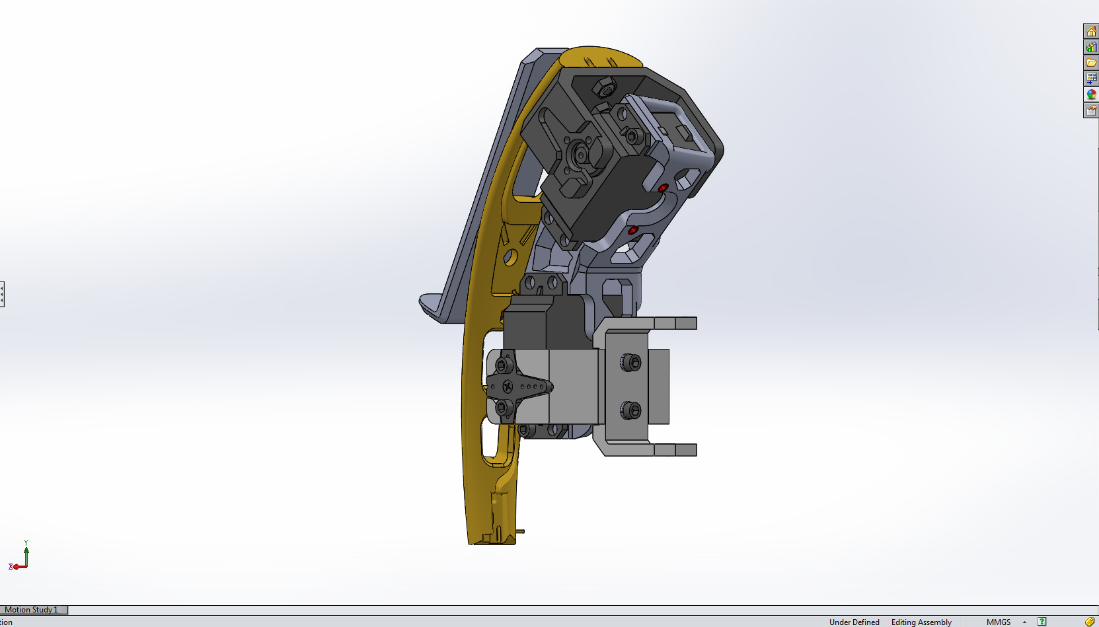
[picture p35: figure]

| Assembly view

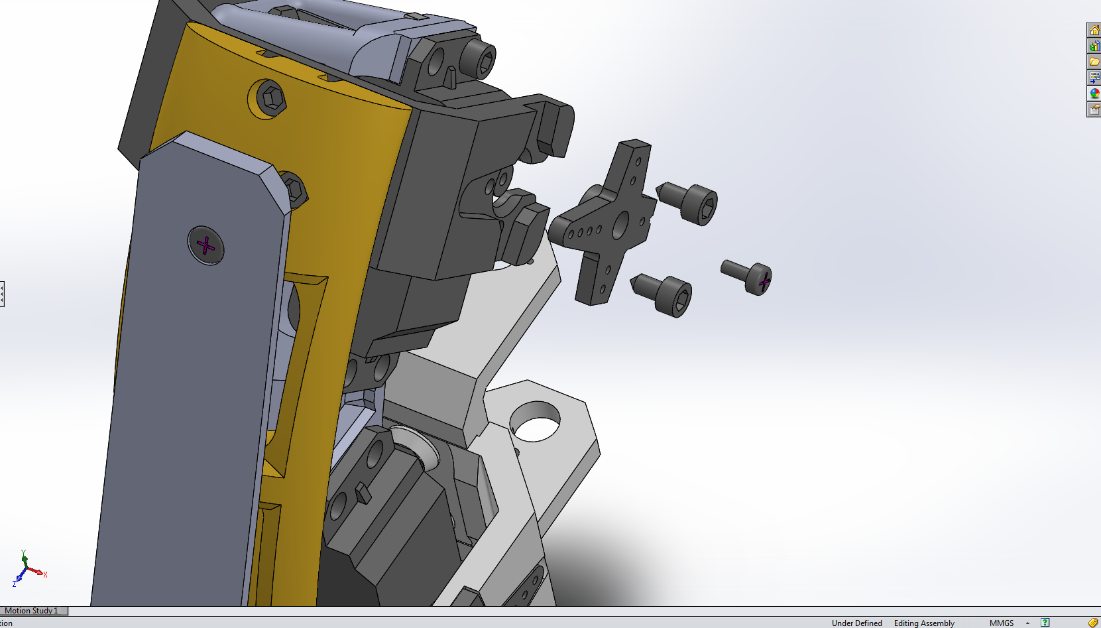
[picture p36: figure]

| (Make sure the servo axle is turned 180o) Servo horn 6mm Hex Self Tapping screws | 1x 2x

MAKII BODY ASSAMBLY 7/25/2020

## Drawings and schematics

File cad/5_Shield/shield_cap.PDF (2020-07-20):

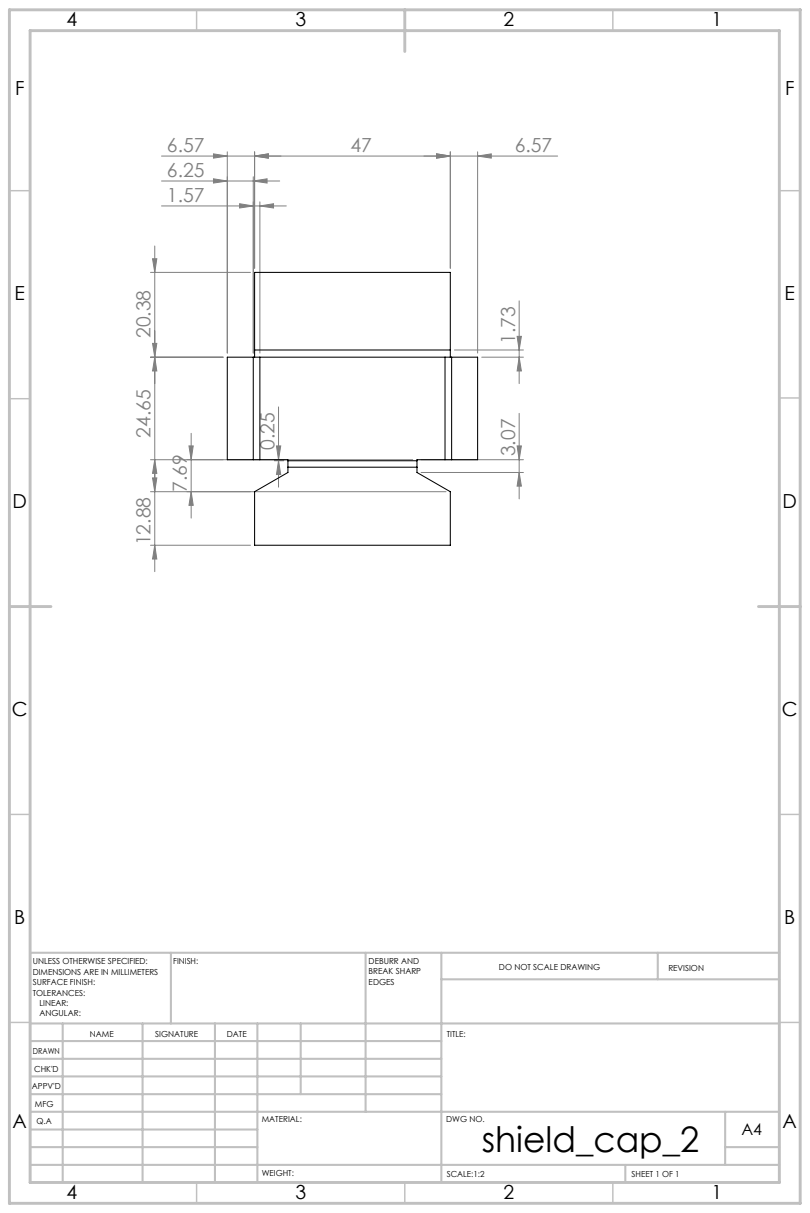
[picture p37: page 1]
FINISH:; DEBURR AND; BREAK SHARP; DO NOT SCALE DRAWING; REVISION; SCALE:1:2; SHEET 1 OF 1

UNLESS OTHERWISE SPECIFIED:
DIMENSIONS ARE IN MILLIMETERS
SURFACE FINISH:
TOLERANCES:
LINEAR:
ANGULAR:

NAME | SIGNATURE | DATE | | | | TITLE:

DRAWN
CHK'D
APPV'D
MFG
Q.A | | | | MATERIAL: | DWG NO. shield_cap_2 | A4

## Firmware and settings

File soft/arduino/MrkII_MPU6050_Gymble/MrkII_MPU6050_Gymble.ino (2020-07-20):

/*
* MASTER Arduino
* Serial communication between container 
* 
* I2C comunication to slaves
* 
*/
#include <RGBLed.h>
/* https://github.com/wilmouths/RGBLed
*/
#include "stdio.h"
#include "I2Cdev.h"
#include "MPU6050_6Axis_MotionApps20.h"

// Arduino Wire library is required if I2Cdev I2CDEV_ARDUINO_WIRE implementation
// is used in I2Cdev.h
#if I2CDEV_IMPLEMENTATION == I2CDEV_ARDUINO_WIRE
#include "Wire.h"
#endif
// ================================================================
// ===               #DEFINE                                    ===
// ================================================================
/* Control keys for reading data
 * ack = enable to read data
 * dis = disable to read data
 *  
 *  the adruino nano will continiue run even when disabled, only the data request is disabled.
 */
#define enableGyroData "ack\n"    // receive confirm 10
#define disableGyroData "dis\n"   // receive confirm 0

#define MAX_OUT_CHARS 16

/* request Gyro data
 *  Yaw   data send i
 *  Pitch data send j
 *  Roll  data send k
 */
#define accesYaw "i\n"
#define accesPitch "j\n"
#define accesRoll "k\n"

#define INTERRUPT_PIN 2  // use pin 2 on Arduino Uno & most boards

// ================================================================
// == Master settings
// ================================================================
/* request head distance data:
 *  demo mode acces with h
 *  
 * request leg sensor data: 
 *  all data update       l
 *  pick serial separated p
 */

#define accesHeadSensor "h\n"
#define accesLegSensor  "l\n"
#define accesLegSeperated "p\n"
/*
 * Define Slave I2C Address
 */
#define HEAD_ADDR 0x06
#define MASTER_ADDR 0x07
#define COMPASS_ADDR 0x08
#define DISTANCE_VALVE 3

// Define counter to count bytes in response
int bcount;
// Define array for return data
int SensorDistance[DISTANCE_VALVE];
int SensorLEGS[8];
int iSensorLEGS;

/*
 * RGB led settings
 */
bool I2C_error = false;
 
#define DATA_SIZE 2
int nucleoData[DATA_SIZE];
int LEG1_DATA[DATA_SIZE];
int LEG2_DATA[DATA_SIZE];
// RGB LED CONFIG
//            RED, GREEN, BLUE
int LEG1_RGB[3] = {11,10,9};
int LEG2_RGB[3] = {6,5,3};

RGBLed led1(LEG1_RGB[0], LEG1_RGB[1], LEG1_RGB[2],COMMON_CATHODE);
RGBLed led2(LEG2_RGB[0], LEG2_RGB[1], LEG2_RGB[2],COMMON_CATHODE);
 
// ================================================================
// == End master settings
// ================================================================


// ================================================================
// == MPU settings
// ================================================================
// class default I2C address is 0x68
// specific I2C addresses may be passed as a parameter here
// AD0 low = 0x68 (default for SparkFun breakout and InvenSense evaluation board)
// AD0 high = 0x69
MPU6050 mpu;
//MPU6050 mpu(0x69); // <-- use for AD0 high

float correct;
int j = 0;

int num = 0;
char  buffer[MAX_OUT_CHARS + 1];

// serial event variable
String inputString = "";      // a String to hold incoming data
bool stringComplete = false;  // whether the string is complete
bool getData = false;

int outp0Value = 0;
int outp1Value = 0;
int outp2Value = 0;

// MPU control/status vars
bool dmpReady = false;  // set true if DMP init was successful
uint8_t mpuIntStatus;   // holds actual interrupt status byte from MPU
uint8_t devStatus;      // return status after each device operation (0 = success, !0 = error)
uint16_t packetSize;    // expected DMP packet size (default is 42 bytes)
uint16_t fifoCount;     // count of all bytes currently in FIFO
uint8_t fifoBuffer[64]; // FIFO storage buffer

// orientation/motion vars
Quaternion q;           // [w, x, y, z]         quaternion container
VectorInt16 aa;         // [x, y, z]            accel sensor measurements
VectorInt16 aaReal;     // [x, y, z]            gravity-free accel sensor measurements
VectorInt16 aaWorld;    // [x, y, z]            world-frame accel sensor measurements
VectorFloat gravity;    // [x, y, z]            gravity vector
float euler[3];         // [psi, theta, phi]    Euler angle container
float ypr[3];           // [yaw, pitch, roll]   yaw/pitch/roll container and gravity vector
float outpValue[3];
// ================================================================
// packet structure for InvenSense teapot demo
// uint8_t teapotPacket[14] = { '$', 0x02, 0, 0, 0, 0, 0, 0, 0, 0, 0x00, 0x00, '\r', '\n' };
// ================================================================


// ================================================================
// ===               INTERRUPT DETECTION ROUTINE                ===
// ================================================================

volatile bool mpuInterrupt = false;     // indicates whether MPU interrupt pin has gone high
void dmpDataReady() {
  mpuInterrupt = true;
}

// ================================================================
// ===                      INITIAL SETUP                       ===
// ================================================================
// reset arduino when does't get an ack
void(* resetFunc) (void) = 0;

void setup() {
  
  // Setup Serial and basic I2C
  // ================================================================
  // join I2C bus (I2Cdev library doesn't do this automatically)
#if I2CDEV_IMPLEMENTATION == I2CDEV_ARDUINO_WIRE
  Wire.begin();
  Wire.setClock(400000); // 400kHz I2C clock. Comment this line if having compilation difficulties
#elif I2CDEV_IMPLEMENTATION == I2CDEV_BUILTIN_FASTWIRE
  Fastwire::setup(400, true);
#endif

  // initialize serial communication
  Serial.begin(115200);
  // reserve 200 bytes for the inputString:
  inputString.reserve(200);
  
  // Setup Gyroscoop
  // ================================================================
  //Serial.println(F("Initializing I2C devices..."));
  mpu.initialize();
  pinMode(INTERRUPT_PIN, INPUT);
  devStatus = mpu.dmpInitialize();
  // supply your own gyro offsets here, scaled for min sensitivity
  mpu.setXGyroOffset(17);
  mpu.setYGyroOffset(-69);
  mpu.setZGyroOffset(27);
  mpu.setZAccelOffset(1551); // 1688 factory default for my test chip

  // make sure it worked (returns 0 if so)
  if (devStatus == 0) {
    // turn on the DMP, now that it's ready
    // Serial.println(F("Enabling DMP..."));
    mpu.setDMPEnabled(true);

    attachInterrupt(digitalPinToInterrupt(INTERRUPT_PIN), dmpDataReady, RISING);
    mpuIntStatus = mpu.getIntStatus();

    // set our DMP Ready flag so the main loop() function knows it's okay to use it
    //Serial.println(F("DMP ready! Waiting for first interrupt..."));
    dmpReady = true;

    // get expected DMP packet size for later comparison
    packetSize = mpu.dmpGetFIFOPacketSize();
  } else {
    // ERROR!
    // 1 = initial memory load failed
    // 2 = DMP configuration updates failed
    // (if it's going to break, usually the code will be 1)
    // Serial.print(F("DMP Initialization failed (code "));
    //Serial.print(devStatus);
    //Serial.println(F(")"));
  }
  Wire.begin(MASTER_ADDR);
  Wire.onReceive(receiveEvent);
}
// ================================================================
// ===                    MAIN PROGRAM LOOP                     ===
// ================================================================
void SetColour();
void CHECK_FLAGS();

void readGyroData();
int readI2C(int);
void readHeadSensorDatarrwd();
void readLegSensorData();

void loop() {
   
  readGyroData();    //READ GYRO DATA 
  
  // send only data on request
  /*
   * IF adruino get an ack\n then 
   * Be active to comunicate by serial
   */
  if (stringComplete){
    //Serial.print(inputString);
    if(inputString == enableGyroData){ //ENABLE: send "ack\n" 
      num = 10;
      sprintf(buffer,"%d",num);
      Serial.println(buffer);
      getData = true;   
    }
    else if(inputString == disableGyroData){ //DISABLE: send "dis\n"
      num = 0;
      sprintf(buffer,"%d",num);
      Serial.println(buffer);
      getData = false; 
    }

    if(getData){
      // == Gyro data ==
      if(inputString == accesYaw){ // I: Send YAW
        //Serial.print("Yaw: ");   
        sprintf(buffer,"%d",outp0Value);
        Serial.println(buffer);
      }
      else if(inputString == accesPitch){ // J: Send Pitch
        //Serial.print("Pitch: "); 
        sprintf(buffer,"%d",outp1Value);
        Serial.println(buffer);
      }
      else if(inputString == accesRoll){ // K: Send Roll
        //Serial.print("Roll: ");  
        sprintf(buffer,"%d",outp2Value);
        Serial.println(buffer);
      } 
      // == End Gyro data ==

      // == Get Slave data on request only ==
      else if(inputString == accesHeadSensor){ //H: Request Head Sensor data
        readHeadSensorData();
        // temporary it's send with tabs in between
        for (int i = 0; i < DISTANCE_VALVE; i++) {
          sprintf(buffer,"%d",SensorDistance[i]);
          Serial.print(buffer);
          Serial.print("\t");
        }
        Serial.println();
      }
      else if(inputString == accesLegSensor){ //L: Request Leg Sensor data
        readLegSensorData();
        // temporary it's send with tabs in between
        for (int i = 0; i < 9; i++) {
          sprintf(buffer,"%d",SensorLEGS[i]);
          Serial.print(buffer);
          Serial.print("\t");
        }
        
        Serial.println();
        iSensorLEGS = 1;
      }
      else if(inputString == accesLegSeperated){ //P: Request Leg Sensor data  
          sprintf(buffer,"%d",SensorLEGS[iSensorLEGS]);
          Serial.println(buffer);
          iSensorLEGS++;
          if(iSensorLEGS > 8){
            iSensorLEGS = 1;
          }
      }
    } 

    // clear inputString and stringComplete
    inputString = "";
    stringComplete = false;
  }
}

void receiveEvent(){
  // clear nucleoData[]
  for(int i = 0; i < DATA_SIZE; i++){
      nucleoData[i] = 0;
  }

  // read incomming data
  while(0< Wire.available()){
    for(int i = 0; i < DATA_SIZE; i++){
      nucleoData[i] = Wire.read();

      if(nucleoData[0] == 1){
        LEG1_DATA[i] = nucleoData[i];
      }
      else if(nucleoData[0] == 2){
        LEG2_DATA[i] = nucleoData[i];
      }
    }
  }
  SetColour();
}

void SetColour(){
  /* 
  Serial.print("LEG3_DATA: \t");
  for(int i =0; i < DATA_SIZE; i++){
    Serial.print(LEG1_DATA[i]);
    Serial.print("\t");
  }
  Serial.println("");  
    
  Serial.print("LEG4_DATA: \t");
  for(int i =0; i < DATA_SIZE; i++){
    Serial.print(LEG2_DATA[i]);
    Serial.print("\t");
  }
  Serial.println("");
  */
  /*
     COLOURS:
    RED        1
    GREEN      2
    BLUE       4
    MAGENTA    8
    CYAN      16
    YELLOW    32
    WHITE     64
  */
  if( LEG1_DATA[0] == 1 && LEG1_DATA[1] == 1){ // blink
    led1.fadeOut(RGBLed::RED,5,100);
  }
  else {
    // LIGHT OFF
      led1.off();
  }
    
  if(LEG2_DATA[0] == 2 && LEG2_DATA[1] == 1){ // blink
    led2.fadeOut(RGBLed::RED,5,100);
  }
  else{
    led2.off();
  }
}

// ================================================================
// ===                    SERIAL EVENT                          ===
// ================================================================
void serialEvent() {
  while (Serial.available()) {
    // get the new byte:
    char inChar = (char)Serial.read();
    // temp print
    //Serial.println(inChar);
    // add it to the inputString:
    inputString += inChar;
    // if the incoming character is a newline, set a flag so the main loop can
    // do something about it:
    if (inChar == '\n') {
      stringComplete = true;
    }
  }
}

// ================================================================
// ===                    I2C EVENT HEAD Sensor                 ===
// ================================================================
void readLegSensorData(){
  /*
  int i = 0;
  while (readI2C(COMPASS_ADDR) < 255) {
  // Until first byte has been received print a waiting message
    delay(100);
    i++;
    if(i >= 20){
      break;
      Serial.println("Error");
    }
  }
  for (bcount = 0; bcount < 9; bcount++) {
    SensorLEGS[bcount] = readI2C(COMPASS_ADDR);
  }  
  */
  Wire.requestFrom(COMPASS_ADDR, 9); 
  int i = 0;
  while(Wire.available()){
    SensorLEGS[i] = Wire.read();
    i++;
  }
}

void readHeadSensorData(){
  int i = 0;
  while (readI2C(HEAD_ADDR) < 255) {
  // Until first byte has been received print a waiting message
    delay(100);
    i++;
    if(i >= 20){
      break;
      Serial.println("Error");
    }
  }
  for (bcount = 0; bcount < DISTANCE_VALVE; bcount++) {
    SensorDistance[bcount] = readI2C(HEAD_ADDR);
  } 
}

int readI2C(int address) {
  // Define a variable to hold byte of data
  int bval;
  long entry = millis();
  
  // Read one byte at a time
  Wire.requestFrom(address, 1); 
  while(Wire.available()== 0 && (millis() - entry) < 100){}
  if(millis() - entry < 200){
    bval = Wire.read();
  }
  return bval;
}

// ================================================================
// ===                    READ GYRO DATA                        ===
// ================================================================

void readGyroData(){
  // if programming failed, don't try to do anything
  if (!dmpReady) return;
  
  // wait for MPU interrupt or extra packet(s) available
  while (!mpuInterrupt && fifoCount < packetSize) {
    if (mpuInterrupt && fifoCount < packetSize) {
      // try to get out of the infinite loop
      fifoCount = mpu.getFIFOCount();
    }
  }
  
  // reset interrupt flag and get INT_STATUS byte
  mpuInterrupt = false;
  mpuIntStatus = mpu.getIntStatus();
  
  // get current FIFO count
  fifoCount = mpu.getFIFOCount();
  
  // check for overflow (this should never happen unless our code is too inefficient)
  if ((mpuIntStatus & _BV(MPU6050_INTERRUPT_FIFO_OFLOW_BIT)) || fifoCount >= 1024) {
    // reset so we can continue cleanly
    mpu.resetFIFO();
    fifoCount = mpu.getFIFOCount();
    //Serial.println(F("FIFO overflow!"));
  
    // otherwise, check for DMP data ready interrupt (this should happen frequently)
  } else if (mpuIntStatus & _BV(MPU6050_INTERRUPT_DMP_INT_BIT)) {
    // wait for correct available data length, should be a VERY short wait
    while (fifoCount < packetSize) fifoCount = mpu.getFIFOCount();
  
    // read a packet from FIFO
    mpu.getFIFOBytes(fifoBuffer, packetSize);
  
    // track FIFO count here in case there is > 1 packet available
    // (this lets us immediately read more without waiting for an interrupt)
    fifoCount -= packetSize;
  
    // Get Yaw, Pitch and Roll values
    mpu.dmpGetQuaternion(&q, fifoBuffer);
    mpu.dmpGetGravity(&gravity, &q);
    mpu.dmpGetYawPitchRoll(ypr, &q, &gravity);
  
    // Yaw, Pitch, Roll values - Radians to degrees
    ypr[0] = ypr[0] * 180 / M_PI;
    ypr[1] = ypr[1] * 180 / M_PI;
    ypr[2] = ypr[2] * 180 / M_PI;
      
    // Skip 300 readings (self-calibration process)
    if (j <= 300) {
      correct = ypr[0]; // Yaw starts at random value, so we capture last value after 300 readings
      j++;
    }
    // After 300 readings
    else {
      ypr[0] = ypr[0] - correct; // Set the Yaw to 0 deg - subtract  the last random Yaw value from the currrent value to make the Yaw 0 degrees
      
      // Map the values of the MPU6050 sensor from -90 to 90 to values suatable for the servo control from 0 to 180
      outp0Value = map(ypr[0], -90, 90, 0, 180);
      outp1Value = map(ypr[1], -90, 90, 0, 180);
      outp2Value = map(ypr[2], -90, 90, 0, 180); 
    }
  } 
}

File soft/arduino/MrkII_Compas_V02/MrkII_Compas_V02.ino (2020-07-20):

/*
 * Update 2.10
 * need new calibration when attached to the robot
 * 
 * >>>>int directionHeading(int heading){
 * 
 * #define DEBUG ENABLES SERIAL INTERFACE
 * #define CALIBRATION show calibration data else it shows direction data
 * #define I2C_ACTIVE ENABLES I2C COMUNICATION
 */ 

//-----INCLUDE-----------*
#include <MechaQMC5883.h>
#include <Wire.h>
#include <math.h>

//-----DEFINE-----------*
#define DEBUG
//#define CALIBRATION
#define I2C_ACTIVE

#define REVISION 2.10
#define DEG_PER_RAD (180.0/3.14159265358979)

// new connection instead of serial

#define SLAVE_ADDR 0x08 // hex 0x10 address for nucleo
#define DATA_SIZE 32

MechaQMC5883 qmc;

//-----VARIABLES----------*
//TEMP:
bool showCal = false;
//------------------------*
bool calibrated = false;
bool calibrationMode = false ;

// I2C
char nucleoData[DATA_SIZE] = "";
bool dataReceived = false;

int x_min;
int x_max;

int y_min;
int y_max;

int z_max;

int x_offset;
int y_offset;

float x_scale;
float y_scale;

String inputString = "";      // a String to hold incoming data
bool stringComplete = false;

int old_spriteNum = 8;
int spriteNum = 0;
//-----SETUP--------------*  
void setup() { 
  #ifdef DEBUG
    Serial.begin(115200);
    Serial.print("REV: ");
    Serial.println(REVISION);
  #endif
  
    Wire.begin();
  #ifdef I2C_ACTIVE
    Wire.begin(SLAVE_ADDR);
    Wire.onRequest(requestEvent);
    Wire.onReceive(receiveEvent);
  #endif
  
  qmc.init();
  inputString.reserve(200);
}

//-----LIST---------------*
void requestEvent(){ Wire.write(spriteNum);}

bool isCalibrated(){ return calibrated;}
bool isCalibrating(){ return calibrationMode;}

float readHeading();
void enterCalNorthMode();

void enterCalMode(); 
void calibrate(); 
void exitCalMode();

int directionHeading(int);

void showDirection(int);
void showCalibration();

//-----MAIN---------------*
void loop() {
  int x, y, z;
  int heading;
  

  // Sensor calibration--------------------------------------------------------
  //---------------------------------------------------------------------------
  //If we're not calibrated
  if(!isCalibrated()){
    
    //And we're not currently calibrating
    if(!isCalibrating()){
      #ifdef DEBUG
        Serial.println("Entering calibration mode");
        Serial.println(">>>> Press h when done....");
      #endif
      enterCalMode(); //This sets the output data rate to the highest possible and puts the mag sensor in active mode
    }
    else{
      //Must call every loop while calibrating to collect calibration data
      //This will automatically exit calibration
      //You can terminate calibration early by calling exitCalMode();
      calibrate(); 
    }
  }
  else if(isCalibrated()){ //isCalibrated(TRUE)
    if(showCal){
      showCal = false;
      showCalibration();
    } 
  }
  
  if(isCalibrated()){
    heading = (int)readHeading();   //reading
    spriteNum = directionHeading(heading);      //get direction
   
    // als new_value = 0 && old value = 7 OF new_value = 7 && old value = 0 >>> OK
    // >> ELSE
      // als new_value - old_value groter dan 1 >>> new_value + 1
      // als new_value - old_value kleiner dan  -1 >>> new value -1

    //if(spriteNum != old_spriteNum){
      
      if((!spriteNum ==0 && !old_spriteNum ==7)||(!spriteNum ==7 && !old_spriteNum ==0)){
        if((spriteNum - old_spriteNum) > 1){
          spriteNum = (old_spriteNum +1);
        }
      }
      else if((spriteNum - old_spriteNum) < -1){
        spriteNum = (old_spriteNum -1);
      }

    /* spriteNum = 0;    // N
     * spriteNum = 1;    // NE
     * spriteNum = 2;    // E
     * spriteNum = 3;    // SE
     * spriteNum = 4;    // S
     * spriteNum = 5;    // SW
     * spriteNum = 6;    // W
     * spriteNum = 7;    // NW
     */
      // show results
      showDirection(spriteNum);

      old_spriteNum =  spriteNum;
      delay(100);
    //}      
  }
}

// SERIAL EVENT----- --------------------------------------------------------
//---------------------------------------------------------------------------
void serialEvent(){
  #ifdef DEBUG
  while(Serial.available()){
    // get the new byte:
    char inChar = (char)Serial.read();
    // add it to the inputString:
    inputString += inChar;
    // if the incoming character is a newline, set a flag so the main loop can
    // do something about it:
    if (inChar == '\n'){
      stringComplete = true;
    }
  }
  #endif
}

// I2C EVENT----- -----------------------------------------------------------
//---------------------------------------------------------------------------
void receiveEvent(){
  
  while(0< Wire.available()){
    for(int i = 0; i < DATA_SIZE; i++){
      nucleoData[i] = Wire.read();
    }
  }
  dataReceived = true;
}

// READING DIRECTION --------------------------------------------------------
//---------------------------------------------------------------------------
float readHeading(){
  int x, y, z;
 
  qmc.read(&x,&y,&z);
  float xf = (float) x * 1.0f;
  float yf = (float) y * 1.0f;
  
  //Calculate the heading
  return (atan2(-y*y_scale, x*x_scale) * DEG_PER_RAD);
}

// CALIBRATION --------------------------------------------------------------
//---------------------------------------------------------------------------
void enterCalMode(){
  calibrationMode = true;
  //Starting values for calibration
  x_min = -20;
  x_max =  10;

  y_min = -20;
  y_max = -10;
 
  z_max = -10;
  calibrated = false;

  /*
   *  Mode : Mode_Standby / Mode_Continuous
   *
   *  ODR : ODR_10Hz / ODR_50Hz / ODR_100Hz / ODR_200Hz
   *  ouput data update rate
   *
   *  RNG : RNG_2G / RNG_8G
   *  magneticfield measurement range
   *
   *  OSR : OSR_512 / OSR_256 / OSR_128 / OSR_64
   *  over sampling rate
  */

  //Set to active mode, highest ODR & OSR for continous readings
  qmc.setMode(Mode_Continuous,ODR_200Hz,RNG_8G,OSR_512);
}

void calibrate(){
  int x, y, z;
  bool changed = false;
  while(!changed){     // wait till robot is ready
    qmc.read(&x,&y,&z);
    
    if(x < x_min){
      x_min = x;
    }
    if(x > x_max){
      x_max = x;
    }
    if(y < y_min){
      y_min = y;
    }
    if(y > y_max){
      y_max = y;
    }
    if(z < z_max){
      z_max = z;
    } 
    
    serialEvent();

    #ifdef I2C_ACTIVE
      receiveEvent();
    #endif
    
    delay(10);
    if((stringComplete && inputString == "h\n") || (nucleoData[0] == 'h')){
      changed = true;
      inputString = "";
      stringComplete =  false;
      dataReceived = false;
    }
  }
   
  exitCalMode();
}

void exitCalMode(){
  //Calculate offsets
  x_offset = (x_min + x_max)/2;

  y_offset = (y_min + y_max)/2;

  x_scale = 1.0/(x_max - x_min);
  y_scale = 1.0/(y_max - y_min);
  
  calibrationMode = false;
  calibrated = true;
  showCal = true;
}
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

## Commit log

2020-07-20 cad update
    [shield_cap_2.SLDDRW, shield_plate.SLDDRW]
2020-07-20 cad main_bodyDesign
    [BODY_PS2Bracket.SLDPRT, BODY_PS2Bracket.STL, BODY_arduinoNanoBracket.SLDPRT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]
2020-07-20 main body
    [BODY_PS2Bracket.SLDPRT, BODY_PS2Bracket.STL, BODY_arduinoNanoBracket.SLDPRT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]
2020-07-20 cad back_bodyDesign
    [CONTAINER_bot.STL, CONTAINER_bracket.STL, CONTAINER_plate.STL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]
2020-07-20 pcb design
2020-07-20 arduino test code
2020-07-25 Add documents
    Changed BOM
    Added tutorial build draft
    [BOM.xlsx]
2020-07-26 Tutorial update
    [BOM.xlsx]
